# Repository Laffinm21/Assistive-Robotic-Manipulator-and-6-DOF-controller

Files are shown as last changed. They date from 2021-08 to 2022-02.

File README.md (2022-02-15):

# Assistive-Robotic-Manipulator-and-6-DOF-controller

Details on this project can also be found on my [Hackaday post](https://hackaday.io/project/181205-assistive-robotic-manipulator-and-6-dof-controller).

## Repository Architecture
This repo is separated into the following folders:
- Mechanical design files
- Software
- Documentation

Demo Video

## Project Background
For those with upper extremity impairments that affect strength and reach, performing simple physical activities of daily life can prove to be insurmountable. Assistive robotic arms have been shown to be effective tools to increase user autonomy within these tasks and can significantly reduce caregiver intervention.[[1]](https://pubmed.ncbi.nlm.nih.gov/22275600/) 

User interfaces for commercial assistive robot arms vary between products, however most are centered around standard wheelchair joysticks or keypads. Such interfaces can lead to a significant bottleneck in user efficiency that is caused by the reality of controlling a high-dimensional robot arm with a low-dimensional "conventional" joystick. That is, without the use of additional intelligent control algorithms, auxiliary buttons and low DoF joysticks are used to switch between control modes to perform compound movements. 

 Such operation is simple however, small delays from switching joints can quickly accumulate into a significant amount of time for the user. The this project is an investigation into the viability of concurrent joint operation, opposed to consecutive operation of individual joints as seen in many current systems. 

## System Overview
Joint angle relationship
Robot Arm and Controller Joystick
The proposed experimental system hardware consists of a robotic arm, a controller arm, and an electronics housing. The controller arm acts as a 6-dimensional joystick, and its pose can be manipulated to proportionally control the robot arm. Calibrating sensitivity of individual joints on the joystick to exploit the user's specific abilities can allow for an increased range of motion of the robot arm. 
Robot Arm and Controller Joystick Early

## Electronics Functional Block Diagram
<p align="center">
  
</p>

## Control Loop diagram
Hybrid control topology

## Controller Arm
An early version of the controller arm is shown below. The device connects to the electronics enclosure via a VGA cable. Each joint rotates about a 10k rotary potentiometer which acts as a position sensor. The kinematic structure of the controller arm is congruent to the robot arm, at approximately 1/3 scale. Each pot acts as a voltage divider and provides an analog voltage for the Teensy to interpret. With full positional and orientationally freedom, users can move the tip of the controller in any direction, and the robotic arm will match the movements in a proportional manner. 
Controller Arm

# Robot Arm
<p align="center">
  
</p>
The design of the robotic arm used in this project is based on the Annin AR3 industrial arm, an open-source robotics platform. More information regarding this project can be found here. The most significant modification to the original design was that I manufactured nearly every component from plastic. There are several reasons why I chose to do this. It is much simpler to machine plastic parts, and building the arm during Covid restricted my access to large equipment that would be necessary to produce an aluminum system. Secondly, a plastic-based robot has generally reduced rigidity, weight and increased compliance compared to aluminum construction. All of these attributes are favorable in application of a collaborative robot (COBOT) where human safety is the top priority.

Completed Arm

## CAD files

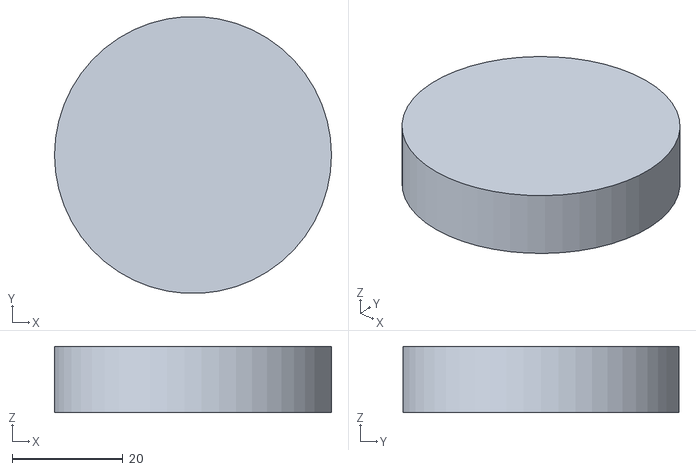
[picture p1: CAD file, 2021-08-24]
Mechanical Design Files/Controller_print_files/J1_spacer_plate.stl
50.0 x 49.9 x 12.0

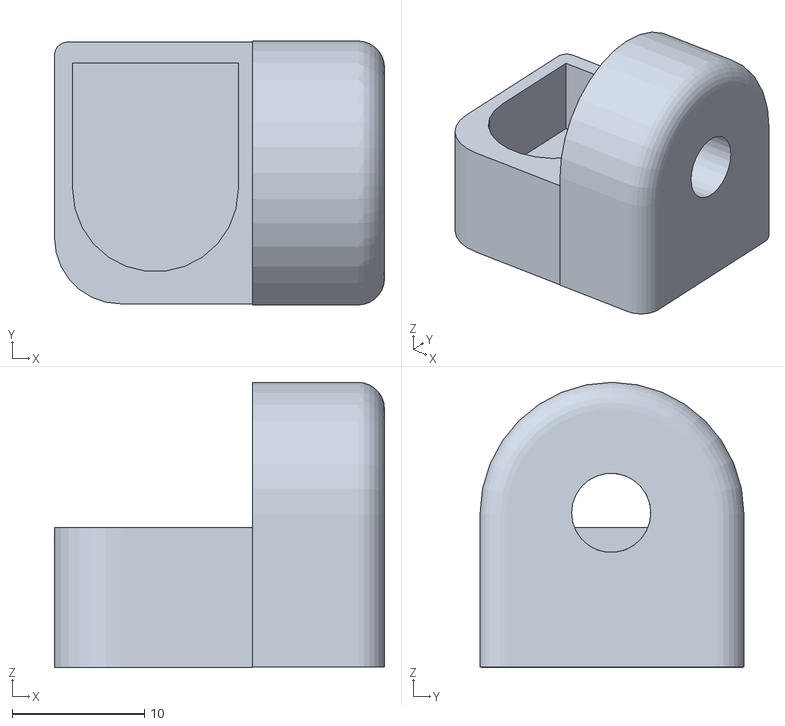
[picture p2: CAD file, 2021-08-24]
Mechanical Design Files/Controller_print_files/J5-J6_hinge.stl
25.0 x 20.0 x 21.6

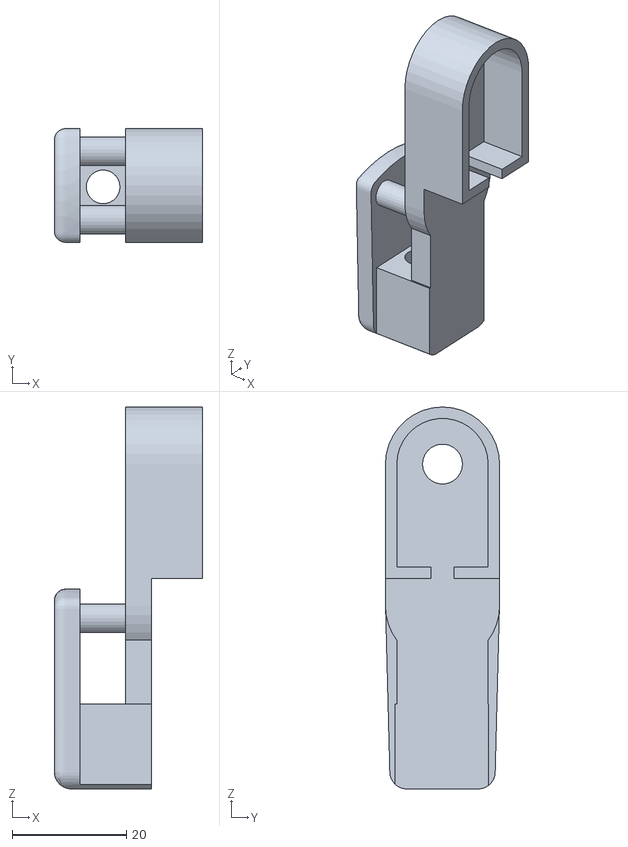
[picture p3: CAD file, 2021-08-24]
Mechanical Design Files/Controller_print_files/J5_arm.stl
26.0 x 20.0 x 66.9

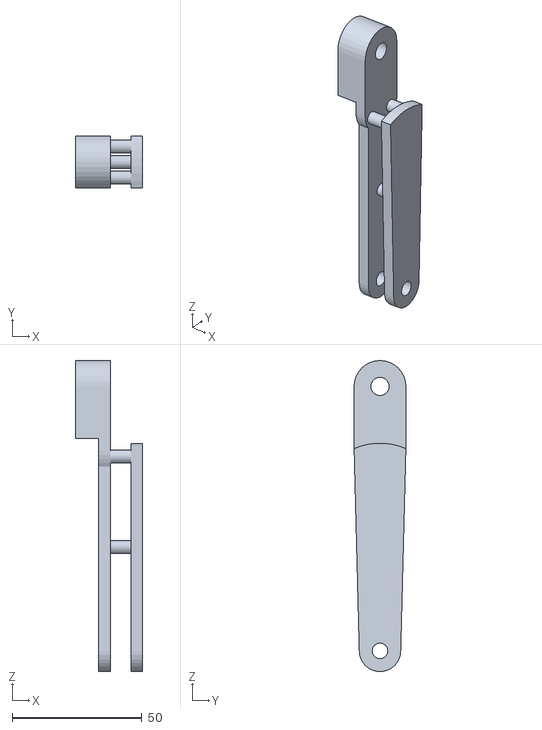
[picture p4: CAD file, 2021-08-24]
Mechanical Design Files/Controller_print_files/J2_arm.stl
26.0 x 20.0 x 120.0

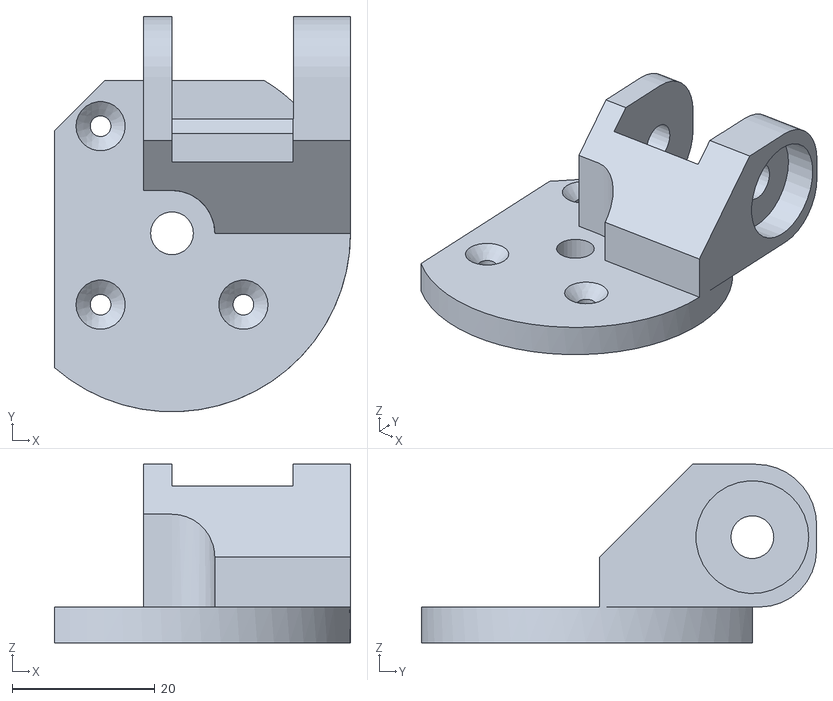
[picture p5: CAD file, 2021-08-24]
Mechanical Design Files/Controller_print_files/J1_turret.stl
41.5 x 55.4 x 25.0

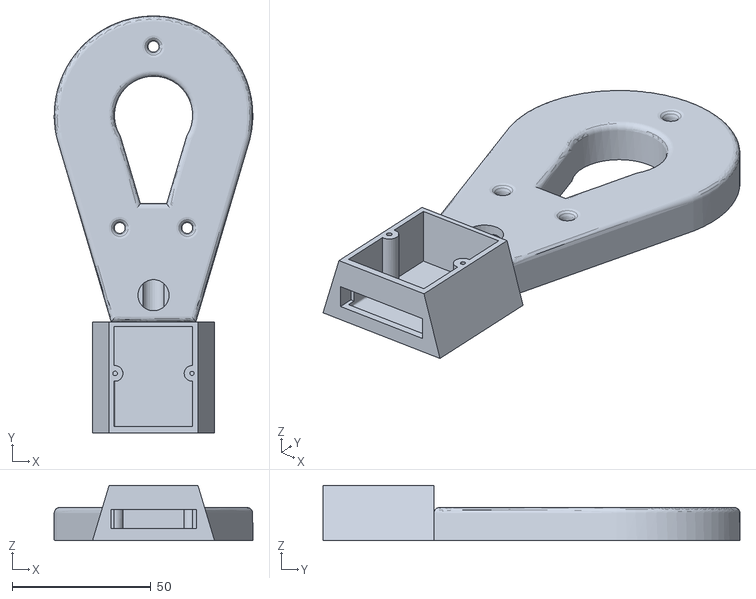
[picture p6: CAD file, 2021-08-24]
Mechanical Design Files/Controller_print_files/Base_cable_housing.stl
71.6 x 150.3 x 20.0

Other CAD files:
Mechanical Design Files/Controller_print_files/J3-J4_hinge.stl

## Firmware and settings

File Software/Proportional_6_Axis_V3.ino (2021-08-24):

#include <AccelStepper.h>
#include <MultiStepper.h>
#define ANALOG_J1 34
#define ANALOG_J2 35 
#define ANALOG_J3 36 
#define ANALOG_J4 37 
#define ANALOG_J5 38 
#define ANALOG_J6 39 
// Input pins for limit switches
#define J1_LIMIT 26
#define J2_LIMIT 27
#define J3_LIMIT 28
#define J4_LIMIT 29
#define J5_LIMIT 30
#define J6_LIMIT 31

AccelStepper J1(AccelStepper::FULL2WIRE, 0, 1);
AccelStepper J2(AccelStepper::FULL2WIRE, 2, 3);
AccelStepper J3(AccelStepper::FULL2WIRE, 4, 5);
AccelStepper J4(AccelStepper::FULL2WIRE, 6, 7);
AccelStepper J5(AccelStepper::FULL2WIRE, 8, 9);
AccelStepper J6(AccelStepper::FULL2WIRE, 10, 11);

const float J1_Mult = 200000; // 10:1 gear reduction, 4:1 pulley ratio, 800 pulses/revolution, 340deg ROM
const float J2_Mult = 30000; // 50:1 gear reduction, 400 pulses/revolution, 132deg ROM
const float J3_Mult = 45000; // 50:1 gear reduction, 400 pulses/revolution, 140deg ROM
const float J4_Mult = 35000; // 10:1 gear reduction, 4:1 pulley ratio, 800 pulses/revolution, 340deg ROM
const float J5_Mult = 20000; // 50:1 gear reduction, 400 pulses/revolution, 132deg ROM
const float J6_Mult = 10000; // 50:1 gear reduction, 400 pulses/revolution, 140deg ROM

void setup()
{
  Serial.begin(9600);
  float J1target = ( 255.0 - ((analogRead(ANALOG_J1) >> 2) / 255.0) * J1_Mult);
  J1.setMaxSpeed(100000);
  J1.setAcceleration(50000);
  J1.moveTo(J1target);

  float J2target = ( 255.0 - ((analogRead(ANALOG_J2) >> 2) / 255.0) * J2_Mult);
  J2.setMaxSpeed(40000);
  J2.setAcceleration(1500);
  J2.moveTo(J2target);

  float J3target = ( 255.0 - ((analogRead(ANALOG_J3) >> 2) / 255.0) * J3_Mult);
  J3.setMaxSpeed(30000);
  J3.setAcceleration(1500);
  J3.moveTo(J3target);

  float J4target = ( 255.0 - ((analogRead(ANALOG_J4) >> 2) / 255.0) * J4_Mult);
  J4.setMaxSpeed(10000);
  J4.setAcceleration(3000);
  J4.moveTo(J4target);

  float J5target = ( 255.0 - ((analogRead(ANALOG_J5) >> 2) / 255.0) * J5_Mult);
  J5.setMaxSpeed(800);
  J5.setAcceleration(100);
  J5.moveTo(J5target);

  float J6target = ( 255.0 - ((analogRead(ANALOG_J6) >> 2) / 255.0) * J6_Mult);
  J6.setMaxSpeed(30000);
  J6.setAcceleration(1000);
  J6.moveTo(J6target);

  pinMode(J1_LIMIT, INPUT);
  pinMode(J2_LIMIT, INPUT);
  pinMode(J3_LIMIT, INPUT);
  pinMode(J4_LIMIT, INPUT);
  pinMode(J5_LIMIT, INPUT);
  pinMode(J6_LIMIT, INPUT);
}

void loop()
{
  if (digitalRead(J1_LIMIT) == HIGH){  // Limit reached
      J1.moveTo((((analogRead(ANALOG_J1) >> 2)- 255.0) / 255.0) * J1_Mult); 
      J1.run(); 
   } else {
      J1.moveTo( 255.0 - ((analogRead(ANALOG_J1) >> 2) / 255.0) * J1_Mult);
      J1.run();
   }
   if (digitalRead(J2_LIMIT) == HIGH){  
      J2.moveTo((((analogRead(ANALOG_J2) >> 2)- 255.0) / 255.0) * J2_Mult); 
      J2.run(); 
   } else {
      J2.moveTo( 255.0 - ((analogRead(ANALOG_J2) >> 2) / 255.0) * J2_Mult);
      J2.run();
   }
  J3.moveTo( 255.0 - ((analogRead(ANALOG_J3) >> 2) / 255.0) * J3_Mult);
  J3.run();
  if (digitalRead(J5_LIMIT) == HIGH){ 
    J4.moveTo(((analogRead(ANALOG_J4) >> 2) / 255.0) * J4_Mult);
    J4.run();
  } else {
    J4.moveTo( 255.0 - ((analogRead(ANALOG_J4) >> 2) / 255.0) * J4_Mult);
    J4.run();
   }
   if (digitalRead(J5_LIMIT) == HIGH){ 
    J5.moveTo(((255.0 - (analogRead(ANALOG_J5) >> 2)- 255.0) / 255.0) * J5_Mult - 225.0);
    J5.run();
   } else {
    J5.moveTo((((analogRead(ANALOG_J5) >> 2)) / 255.0) * J5_Mult - 255.0);
    J5.run(); 
   }
  J6.moveTo( 255.0 - ((analogRead(ANALOG_J6) >> 2) / 255.0) * J6_Mult);
  J6.run();
  
  Serial.print("ANALOG_J5: ");
  Serial.print(analogRead(ANALOG_J5));
  Serial.print("  J5.currentPosition(): ");
  Serial.print(J5.currentPosition());
  Serial.print("  J5.targetPosition(): ");
  Serial.println(J5.targetPosition());
}
